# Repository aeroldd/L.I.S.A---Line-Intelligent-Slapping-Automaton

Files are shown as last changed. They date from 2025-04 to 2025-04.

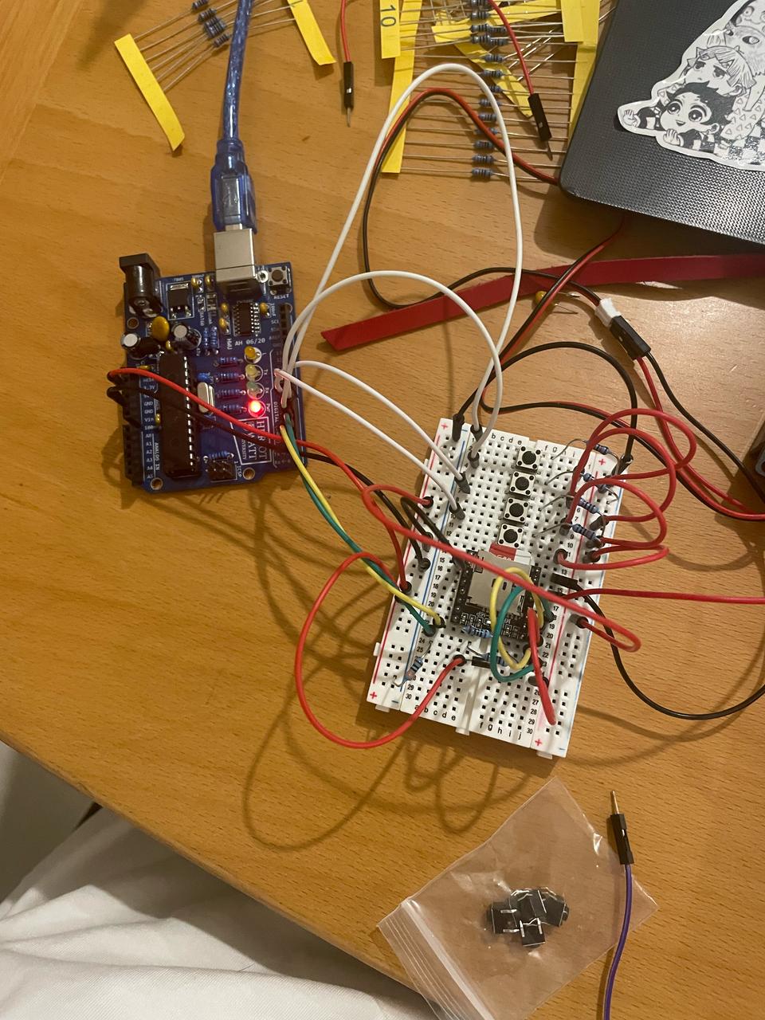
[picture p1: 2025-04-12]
Pictures/090325-DFPlayerMiniTestingB.jpg

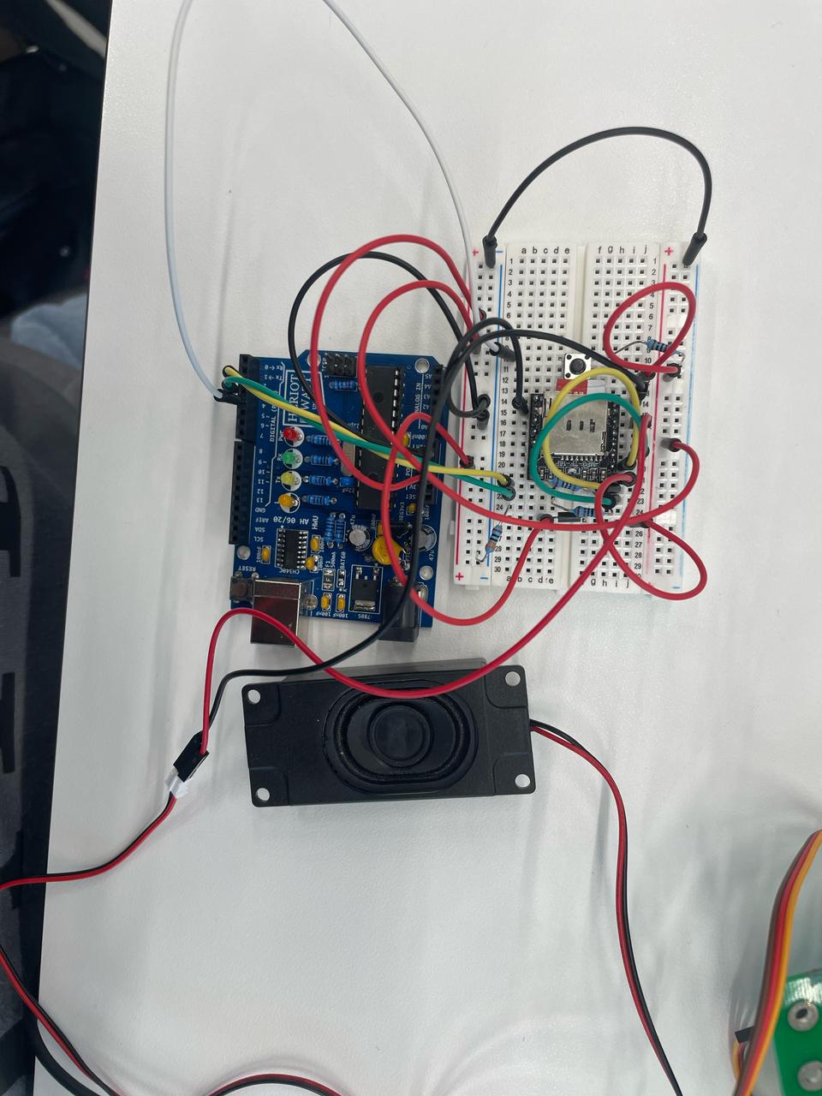
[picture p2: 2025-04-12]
Pictures/100325-DFPlayerMiniTesting.jpg

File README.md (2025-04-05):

L.I.S.A - Your Line Intelligent Slapping Automaton

Aerold Parcon and Anas Gomaa's brain child (Heriot Watt University - 1st Year Robotics Group Project B37VR Final Project)

Meet L.I.S.A - an intelligent robot controlled by an Arduino Uno that:
- Follows lines with a high degree of accuracy and precision
- Avoids obstacles by slapping them out of her way
- Has audio and visual cues to show what its doing
- Has lots of attitude

This repository houses all:
- All of L.I.S.A's brains (Arduino sketches used to control L.I.S.A's systems)
- Testing code and all the individual systems used in designing the final source code
- Sketches, CAD files and diagrams of the body and chasis
- Schematics of all sorts (Circuits, systems, etc)
- Your personal - How to make your own L.I.S.A instruction handbook.
- L.I.S.A care guide

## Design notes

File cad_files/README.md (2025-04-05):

THE CAD FILES OF L.I.S.A's Body and other printed parts

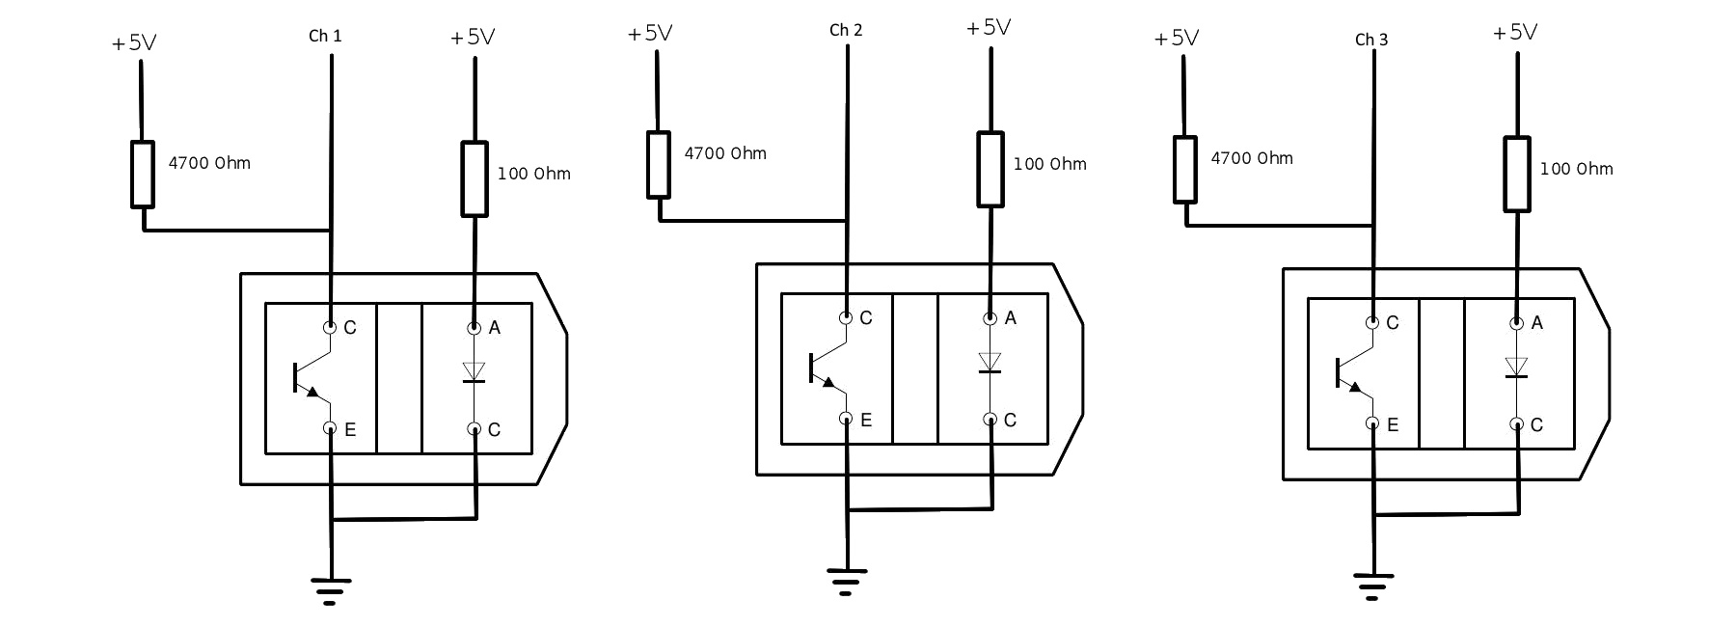
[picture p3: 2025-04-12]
Schematics/line follower module schematic.jpg

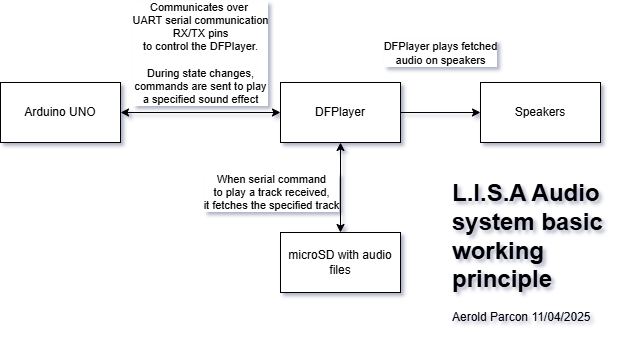
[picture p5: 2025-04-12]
Schematics/lisa_audio_system_blocks.drawio.png

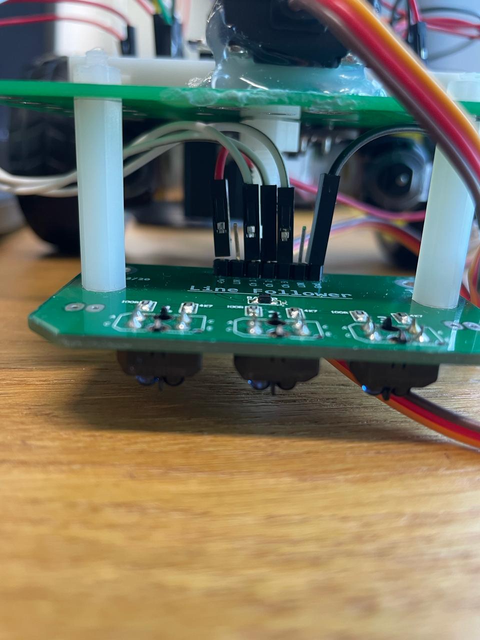
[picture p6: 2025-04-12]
Pictures/130325-LineFollowerPCBConnectedA.jpg

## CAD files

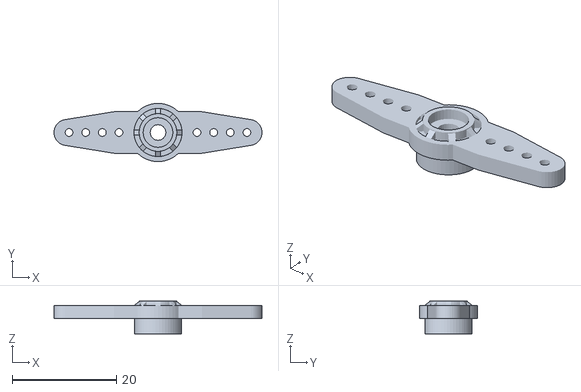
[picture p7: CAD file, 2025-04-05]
cad_files/mg996_arm_2pad.stl
40.0 x 11.2 x 6.30

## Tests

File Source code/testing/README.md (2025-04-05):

The main sketches used in the testing and calibration of L.I.S.A's development and prototyping time

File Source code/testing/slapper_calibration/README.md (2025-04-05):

SLAPPER CALIBRATION
This sketch is used to calibrate the minimum and maximum angle for slapping in L.I.S.A's obstacle avoidance system.
The right minimum and maximum angles must be determined so that the internal support structures in the chasis wouldnt get slapped on the way.

This sketch uses a potentiometer to set the angle and a button to confirm the angle
Once the program is finished running, the program prints out the minimum and maximum angles of the slap.
These values will be used in the slapper arm in the final L.I.S.A source code.

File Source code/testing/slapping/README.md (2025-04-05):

This sketch was used in testing the slapping mechanism of L.I.S.A.

Uses an ultrasonic sensor -> gets the distance -> if the distance is in the sapping threshold, it will slap the object infront of it.

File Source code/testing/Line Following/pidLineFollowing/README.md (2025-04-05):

/*
PID implemented Line following control of two Bi-directional Motors

This sketch was used to test if PID line following was better to use instead of a standard line
following agorithm - which it was

*/
// WheelDrive - move a pair of DC motors at varying rate and direction
//
// Copyright (c) 2016, Garth Zeglin.  All rights reserved. Licensed under the
// terms of the BSD 3-clause license as included in LICENSE.
//
// This program assumes that:
//
//  1. A DRV8833 dual DC motor driver module is connected to pins 5, 6, 9, and 10.
//  2. A pair of motors is attached to the driver.
//  3. The serial console on the Arduino IDE is set to 9600 baud communications speed.

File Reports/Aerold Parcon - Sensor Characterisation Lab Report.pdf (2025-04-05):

B37VR Robotics Group Project, Sensor characterisation report

# Heriot-Watt University Dubai

### B37VR Robotics Group Project, Year 1

## IR Sensor Characterisation Report

Student’s name | Aerold Parcon
Student ID | H00448855
Professor’s name | Dr Girish Balasubramanian
Buggy Number | B8

## Abstract

IR sensors are the eyes of an autonomous line following robot. The sensor’s characteristics must be understood to find the right thresholds of what the robot considers a line to follow. The experiments aimed to investigate IR sensor readings on different types of surfaces – grey floor, clean black tape and dirty black tape - and under different lighting conditions. An Arduino program was used to read the three IR sensor’s values. The results found that black tape, whether clean or dirty, produce a higher IR sensor reading than the grey floor. Increased ambient lighting increased the sensor reading in the grey floor, however this wasn’t observed in all surfaces, due to uncontrolled ambient lighting. The line following threshold values were found – the line is detected on values above 674. However, with the limited setup, the effects of ambient light and distance couldn’t be found.

## Contents

## Introduction

IR sensors are a core component of an autonomous line following robot. It serves as the ‘eyes’ of the robot, determining where the line is, and sends the recorded data to the Arduino Uno microcontroller which computes and updates the direction of the buggy. The TCRT5000 sensor used in this experiment is a reflective sensor which includes an infrared emitter and a phototransistor [1], and detects black lines by determining the amount of light which is reflected back (black absorbing more light than other surfaces).

In order to detect lines, a threshold of what is a black surface must be determined. This lab report aims to characterise the TCRT5000 sensor to determine the analog read values of different surfaces to define the sensing threshold of the black line to be followed and to analyse how the sensor’s readings are affected by different variables such as ambient light, the quality and texture of the surface. By the end of these series of experiments, the sensor’s characteristics will be determined and understood and the appropriate line reading threshold will be found.

Objectives:

- Understand the working principle of the TCRT5000 IR sensor.
- Test different surfaces against the IR sensor and find the right threshold for line following.
- Evaluate the effects of ambient lighting on the accuracy of the IR sensor.

## Background Theory - How IR sensors work and how it can detect lines

As briefly mentioned in the introduction, the TCRT5000 sensor is a reflective optical sensor with a transistor output, including an infrared emitter and a phototransistor [1].

The diagram below (Figure 2.1) is the circuit schematic of the sensor and how its used to read values.

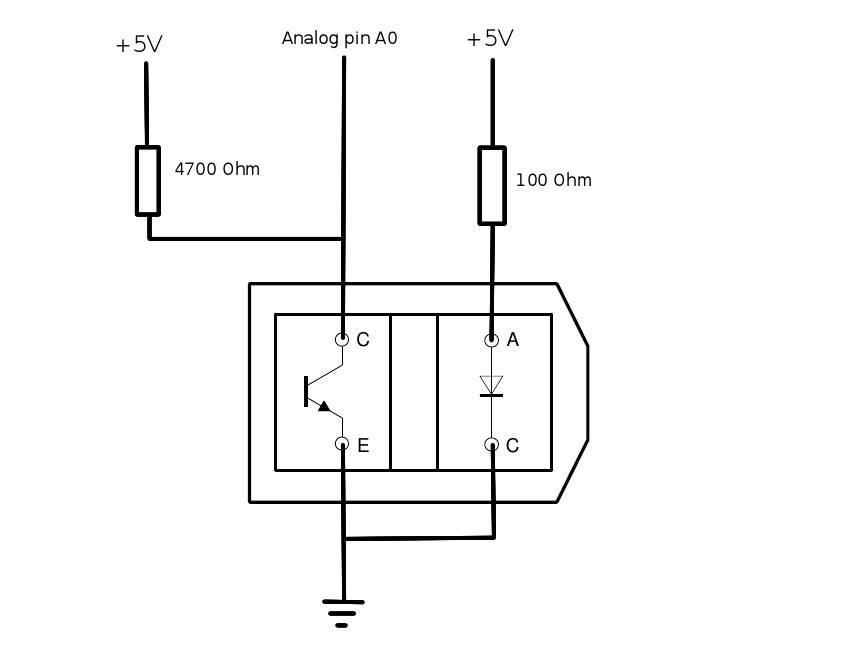
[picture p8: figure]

Figure 2.1: Top-down schematic view of the IR sensor, and how its connected to the Arduino analog pin A0 to read the sensor. [2]

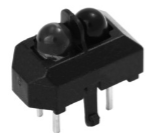
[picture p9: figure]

Figure 2.2: The TCRT5000 sensor. The black wall between the phototransistor and the IR LED blocks the emissions directly from the LED so that it can only detect the waves reflected back by surfaces. Image from the data sheet [1].

Essentially, the LED between points A and C shown on the figure above is an Infrared LED which emits a wave of 950nm [1]. The wave is emitted and is reflected on a surface, back to the sensor. The phototransistor detects the reflected infrared light – when light falls on the transistor, the atoms in the collector region become excited and emit free electrons [3], allowing current to flow through from the collector to the emitter. Therefore, as more light is detected, more atoms get excited and more electrons are freed, allowing more conductivity. This will cause more current to flow to the ground. This reduces the output voltage at point C, producing lower values.

In summary:

- IR LED emits light
- Light reflected and sensed by the phototransistor
- When the transistor detects light – more current flows to ground, less current flows to analog pin
- Therefore, more light = smaller reading; less light = greater reading.

## Methodology

In this lab report, various experiments were taken to characterise the IR sensor under different operating conditions - types of surfaces, and how the sensor reacts to different environmental ambient lighting. With the results gathered from these experiments, the line following threshold can be found.

Experimental setup

The following experiments were done using the Robotics Group Project buggy (Figure 3.1) provided by the course. It includes an Arduino Uno microcontroller, a breadboard for connections, an H-Bridge motor driver and a pair of motors (not used in this experiment), and a line following module – a PCB consisting of three TCRT5000 sensors, which are going to be characterised in these experiments.

The following connections were made (as shown on figure 3.2). 5V connected to the +5V pin on the Line Follower, channel 1, 2 and 3 connected to analog pins A3, A4 and A5 respectively and GND connected to GND. The fully wired IR sensor reading setup is shown on figure 3.3 below.

Figure 3.1: Arduino buggy used in this experiment. Other connections and modules were connected to the Arduino for other functionalities in the line following buggy – these can be ignored.

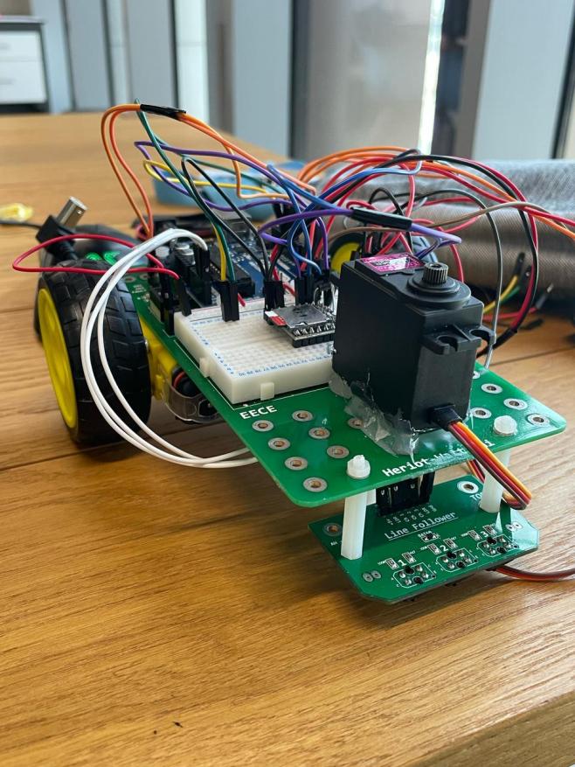
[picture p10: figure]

Figure 3.2: Schematic diagram of the IR sensor reading experimental setup.

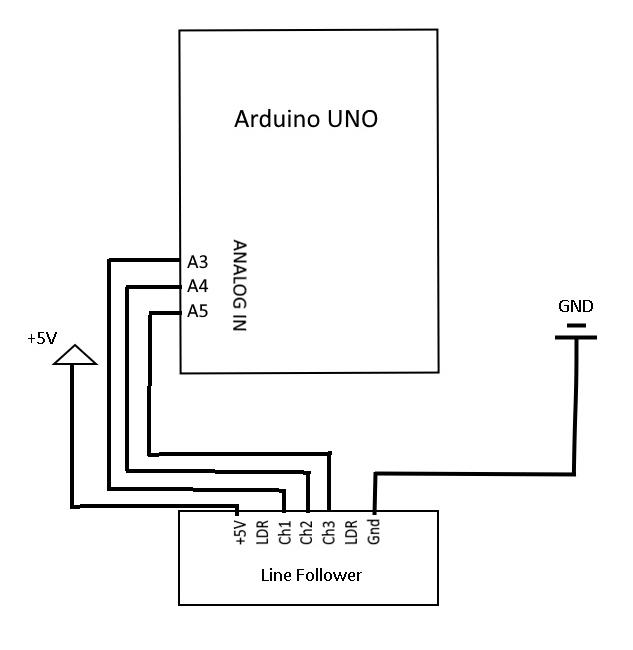
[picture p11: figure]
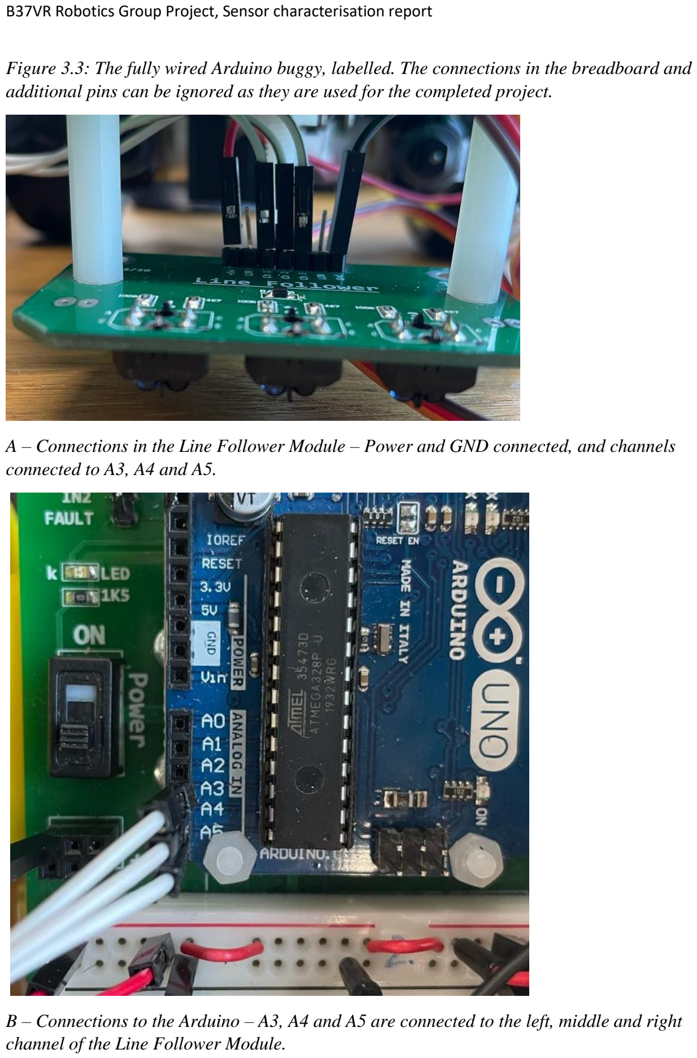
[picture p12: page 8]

Figure 3.3: The fully wired Arduino buggy, labelled. The connections in the breadboard and additional pins can be ignored as they are used for the completed project.

A – Connections in the Line Follower Module – Power and GND connected, and channels connected to A3, A4 and A5.

B – Connections to the Arduino – A3, A4 and A5 are connected to the left, middle and right channel of the Line Follower Module.

The Line Follower PCB
As previously mentioned, the three TCRT5000 sensors are soldered onto a PCB. The schematic diagram of the Line Follower module is attached on Appendix A. In summary, channel 1, 2 and 3 is connected to the collector pins of the left, centre and right sensors, and these are connected to the Arduino Uno’s A3, A4 and A5 analog pins.

Arduino code – IRSensorRead.ino

The sketch IRSensorRead.ino (full code available on Appendix B) is uploaded onto the Arduino Uno. It reads each channel’s analog output using analogRead(), an inbuilt function which reads the voltage in the analog pins as a value between 0-1023 bits. To convert this value into voltage, the following equation can be used:

V =

Analog read value + 1
1024

× 5

The program outputs the values in the format <left value>,<middle value>,<right value> on the Serial Monitor, which can be easily copied and pasted into a .csv file, which can later be opened in Excel for data analysis.

Surfaces

Figure 3.4: The different surfaces that will be tested in the experiments.

Type of Surface | Reason
Grey floor of robotics lab | Line following buggy demonstration will be carried out on the floor of the Robotics lab.
Glossy black electrical tape | Line following buggy designed to follow standard glossy black electrical tape on the floor of the Robotics lab.
Dirty dull black electrical tape | To test the tolerances the threshold should include. There may be imperfections in the line, so a dirty dulled out black electrical tape can serve as an extreme corner case for imperfections.

Figures 3.5 – 3.7 are pictures of the surfaces measured in this experiment.

Figure 3.5: Grey floor of the Robotics Laboratory

Figure 3.6: Clean black tape

Figure 3.7: Dirty black tape

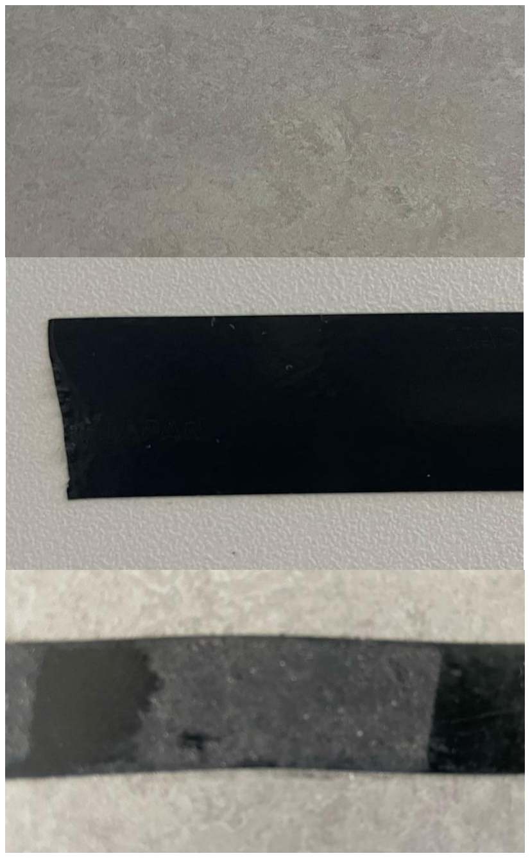
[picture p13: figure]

For the setup used in the experiments, strips of tape were placed on the ground.

Ambient lighting

To measure the IR sensors’ readings, the environment had to be as controlled as possible – the background lighting of a room interferes with the IR sensor readings. The ambient light had to be controlled as much as possible. Ideally, a totally dark environment should be used to eliminate the variable of ambient lighting. However, there were no totally dark areas in university where the experiment could be done, so two different light settings were chosen – dim and bright.

In previous experiments, the light intensity was measured with a luxmeter [4], and the correlation between light intensity and accuracy was found. However, due to limited resources, no light intensities could be quantified.

Lighting | Description
Dim | All lights in the Robotics Lab were dimmed to the lowest possible setting. Blinds and curtains were fully closed. The experiment was set up in a place far away from windows and other potential light sources.
Bright | All lights in the lab were set to the brightest setting. Blinds and curtains were fully drawn open to let as much sunlight in. However, the experiment was done in the same place so that the surfaces will be the same.

Figure 3.5: Two different lighting conditions that were controlled.

Distance

Initially, the effect of height on the IR sensor’s readings were to be investigated to find the optimal distance of the IR sensor from the ground for line following. Previous experiments [4] on IR sensor characteristics have done this using a custom-made jig, to measure the effects of distance to accuracy and precision. However, with the limited resources available, there were no ways to change the height accurately. In previous attempts, soldering helping hands were used to suspend the sensor and change the heights, but there was no proper way to repeat heights for experiments as there was a lot of human error – the angle, positioning, different heights, etc.

For this experiment, height was kept constant by attaching the Light Follower module to the buggy. This will be the same height used for line following, so it was practical.

Procedure

The experiment was first setup as described above – Code uploaded onto the Arduino, connections between the analog pins and the Line Follower module’s channels were made, surfaces were laid out, and ambient lighting were set.

The first experiment’s goal was to determine the IR sensors’ readings on each surface in the controlled dim light environment.

1) The readings for the floor were tested. The program was allowed to loop until approximately 20 sets of values were on the Serial Monitor in Arduino IDE.
2) These values were copied and recorded onto a CSV file.
3) This is repeated for the different surfaces – the clean glossy black electrical tape, and the dull dirty black electrical tape.

The second experiment’s goal was to investigate the effects of ambient room lighting on the IR sensors’ readings. The first experiment was repeated, but this time, instead of having the room’s lights dimmed, the lights were maximised to the brightest setting, and the windows were drawn open.

## Results

This section of the report presents the results of the IR sensor characterisation experiments, showing the effects of surface type and ambient light on the three sensors’ readings. The collected data (raw data available on Appendix C) includes the type of surface, the ambient lighting of the room, the average analog pin readings from the sensor, the average voltage, the minimum and maximum readings and standard deviation. The key findings are summarised in figures 4.1 to 4.4 below.

Figure 4.1: The effects of ambient lighting and surface type on IR sensor readings

Ambient Lighting | Surface type | Mean analog pin reading | Minimum analog pin reading | Maximum analog pin reading | Range
dim | Grey floor | 413.03 | 360.00 | 489.00 | 129
dim | Black tape (clean) | 865.23 | 838.00 | 899.00 | 81
dim | Black tape (dirty) | 905.73 | 802.00 | 965.00 | 163
bright | Grey floor | 436.39 | 373.00 | 541.00 | 168
bright | Black tape (clean) | 855.26 | 826.00 | 882.00 | 56
bright | Black tape (dirty) | 818.13 | 710.00 | 946.00 | 236

Figure 4.2: A minimum-maximum chart comparing the effects of lighting and surface on the IR sensor readings.

The standard deviation of the analog readings provides a measure of the IR sensor’s precision under different working conditions.

Figure 4.3: The average standard deviation of analog readings depending on the lighting and surface conditions.

Lighting Surface Average standard
deviation | Range
dim | grey | 0.88 | 129
dim | clean | 2.79 | 81
dim | dirty | 8.75 | 163
bright | grey | 1.24 | 168
bright | clean | 1.05 | 56
bright | dirty | 2.41 | 236
413.03 | 436.39
865.23 | 855.26

905.73

818.13

360 | 373
838 | 826 | 802

710

489

541

899 | 882
965 | 946

300.00

400.00

500.00

600.00

700.00

800.00

900.00

1000.00

dim | bright | dim | bright | dim | bright
grey floor | black tape (clean) | black tape (dirty)

### Effect of ambient light and surface type on IR sensor analog readings

Mean | Min | Max

Figure 4.4: The average standard deviations, graphed.

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
dim | bright | dim | bright | dim | bright
grey floor | black tape (clean) | black tape (dirty)

### Average standard deviation

## Discussion

This study investigated the effects of ambient background lighting and surface conditions on IR sensor readings. The results show that the sensor readings varied significantly based on the different factors – ambient lighting and surface type.

The results support the initial hypothesis - both clean and dirty black tape yielded higher readings than the floor as they reflect less light back. For example, when under dim light conditions, the floor returned an average reading of 413.03, compared to the higher readings of clean (865.23) and dirty black tape (905.73). Surface colour does affect the amount of infrared radiation absorbed as previously hypothesised, however, the type of surface – the reflectivity and smoothness – should also be accounted for. The black tape has a glossy finish which makes it act essentially as a mirror. Mirror reflection occurs when light strikes surfaces that are smooth or glossy, like the glossy black tape, reflecting at the opposite direction from the source [5]. Though the tape was glossy, because it was black, more infrared light was absorbed, hence giving a higher reading.

The uniformity and texture of the surface influences the IR sensor readings. The sensor readings were different when testing out clean and dirty tape surfaces. Under dim light conditions, the clean tape produced an average reading of 865.23, whereas the dirtier tape returned an average reading of 905.73. This is because the different dust and dirt particles in the dirty tape creates an uneven surface with different heights and colours, causing light to reflect in different directions, therefore less light is detected by the sensor.

The dirtier tape provided a greater range of readings, proving the influence surface texture has on sensor precision and accuracy. The clean tape has an average standard deviation of 2.76, while the dirty black tape has an average standard deviation 8.75, meaning that it read a wider range of values. As previously mentioned, this is because of the uneven surface with different heights, colours and reflectivity because of dust and dirt particles, reflecting light in different directions, which gives a wider range of values.

Different ambient light conditions affect sensor readings. For the grey floor, brighter room conditions increased the sensor readings compared to the dimmer room. Under dim light, the sensor read 413.03 on average, and under brighter light, the sensor read 436.39. Hypothetically, the reading should be lower because the IR sensor would detect more light from the environment, but that isn’t the case. This can be an anomalous reading. For the other surfaces, the results were as expected – for the clean black tape, it read 865.23 in dim light decreasing to 855.26 in bright light. This is because more IR light is detected from the surroundings, hence the lower reading. This is similar for the dirty tape (905.73 in dim, 818.13 in bright).

Interestingly, brighter room conditions increased the precision of reading black tape readings. Under dim light, the clean and dirty tape, had average standard deviations of the clean and dirty black tape were 2.79 and 8.75 respectively. Comparatively, under bright light, the clean and dirty tape, on average, had standard deviations of 1.05 and 2.41. The inconsistencies of the readings could be because the ambient lighting in the room couldn’t be perfectly controlled – non-uniform lighting, large windows on two sides of the room, position of the sun in the experiment, shadows, flickering room lights, etc. Therefore, the results fail to establish a relationship between ambient light and the precision and readings of the IR sensors – showing the importance of having a controlled laboratory environment for future iterations of this experiment.

For future experiments to investigate the effect of ambient light, a luxmeter should be used to measure the actual lighting on the room and find a correlation between the ambient lighting and sensor noise. A controlled environment where the lighting can be controlled should be used. To test the IR sensors without ambient light interference, the experiment must be done in a dark room.

Using the results, the global minimum and maximum thresholds for detecting surfaces can be finally determined. This is displayed on figure 5.1.

Figure 5.1: The line following thresholds.

Surface | Min | Max | Min -5% | Max+5%
Floor | 360.00 | 541.00 | 342 | 568
Line | 710.00 | 965.00 | 674 | 1013

## Conclusion

The aim of this lab report was to characterise a set of IR sensors to calibrate it and find an appropriate threshold for line detection for the line following buggy. The experiments and research carried out in this study successfully provided insight on the working principles of how IR sensors can be used to detect lines for an autonomous line following robot. The experiments aimed to investigate the influence of surfaces and ambient lighting on IR sensor readings, and it concluded that darker surfaces reflect less light, producing a greater IR sensor reading. With the limited experimental setup, the effects of ambient lighting on the IR sensor’s precision couldn’t be properly investigated as the room’s lighting couldn’t be quantified.

The ideal line detection thresholds have been successfully found in this experiment. This can be applied to the line following code to ensure precise line detection.

For future iterations of this study, a controlled environment where the ambient lighting can be measured and tweaked should be used to mitigate the errors caused by uncontrolled ambient light. Additionally, conducting the test in a fully darkened room can stop the ambient IR interference, or enclose it in a box. A lux meter should be used to measure the light intensity of ambient light.

Studying the effects of distance and angle from the surface can provide further insight to how it affects IR sensor readings, and using the results from the testing can give the ideal sensor position for line following, sensor sensitivity, noise and precision.

Now that the IR sensors were characterised, it can be used to make an autonomous line following robot.

## References

[1] Vishay Semiconductors (2009). TCRT5000, TCRT5000L Data sheet - Reflective Optical Sensor with Transistor Output. [Component data sheet] [Online] Available at: https://www.vishay.com/docs/83760/tcrt5000.pdf (Accessed at: 7th March 2025).
[2] B37VR Robotics Group Project (2025). TCRT5000 connection diagram - tcrt5000-connection.jpg. [Canvas] Available at: tcrt5000-connection.jpg. (https://canvas.hw.ac.uk/courses/27298/files/3903260/download?wrap=1) (Accessed at: 7th March 2025).
[3] Bishop, O. (2001) ‘Optoelectric Sensors’, in Understand Electronics. Newnes, pp. 131–137.
[4] B. Azzopardi, E. Dimech, A. Sammut and A. Mifsud (2023). "Characterisation of Infrared Sensors for Close-Proximity Distance Measurement," IECON 2023- 49th Annual Conference of the IEEE Industrial Electronics Society, Singapore, Singapore. pp. 1-6. Available at: doi 10.1109/IECON51785.2023.10312588. (Accessed at 11th Match 2025)
[4] 3M (2004) Reflectivity flyer, [Flyer] [Online PDF] Available at: https://multimedia.3m.com/mws/media/295767O/reflectivity-flyer.pdf. (Accessed at: 13th March 2025).

## Appendix

Appendix A – Line Follower PCB circuit diagram

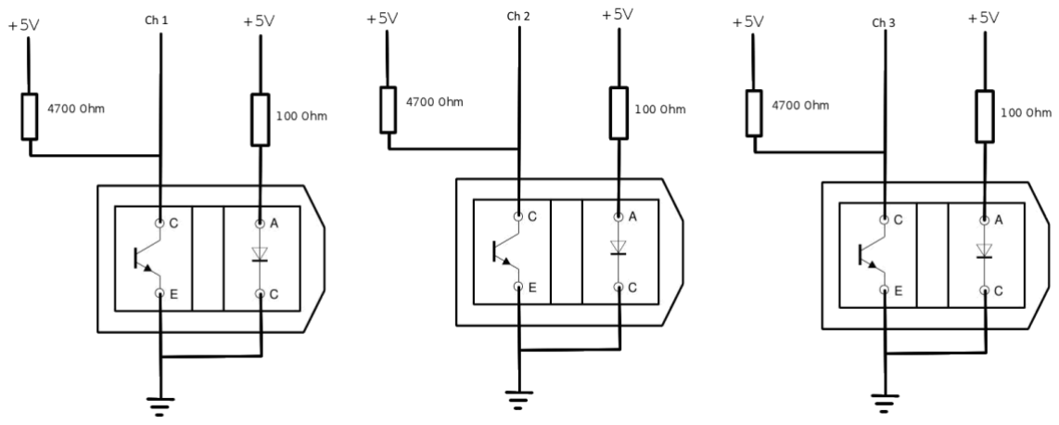
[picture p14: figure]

Figure A.1: Line Follower PCB circuit diagram. Consists of three IR sensors next to each other, and has pins Ch 1, Ch 2 and Ch 3 which are connected to the Arduino.

Appendix B – IRSensorRead.ino
The code below is a modified version of the sketchIRsensorRead.txt code taken from Canvas – changing it so that the printed values are in a .csv format for ease of data analysis in Excel.

/*
Read 3 IR sensors for callibration
*/
// Read 3 IR sensors for callibration //
/*
AnalogReadSerial

Reads an analog input on pin 3,4 &5, prints the result to the Serial Monitor. Graphical representation is available using Serial Plotter (Tools > Serial Plotter menu).

Adapted from the example code is in the public domain.

http://www.arduino.cc/en/Tutorial/AnalogReadSerial
*/

// the setup routine runs once when you press reset:
void setup() {
// initialize serial communication at 9600 bits per second: Serial.begin(9600);
}

// the loop routine runs over and over again forever: void loop() {
// read the input on analog pin 0:
int sensorValueLeft = analogRead(A5);
delay(2);
int sensorValueCentre = analogRead(A4); delay(2);
int sensorValueRight = analogRead(A3); delay(2);
// print out the value you read: Serial.print("");
Serial.print(sensorValueLeft); Serial.print(",");
Serial.print(sensorValueCentre); Serial.print(",");
Serial.println(sensorValueRight);
delay(1000); | // delay in between reads
}

Appendix C: Raw data summary
Sensor Position | Lighting | Surface | Average analog reading | Standard deviation | Voltage (average) | Min | Max
left | dim | Grey floor | 362.00 | 0.97 | 1.77 | 360.00 | 365.00
| | Clean black tape | 846.56 | 2.85 | 4.13 | 838.00 | 852.00
| | Dirty black tape | 833.70 | 8.81 | 4.07 | 802.00 | 840.00
| bright | Grey floor | 374.90 | 1.58 | 1.83 | 373.00 | 382.00
| | Clean black tape | 828.72 | 1.05 | 4.05 | 826.00 | 831.00
| | Dirty black tape | 795.63 | 3.22 | 3.88 | 784.00 | 799.00
middle | dim | Grey floor | 390.00 | 0.89 | 1.90 | 389.00 | 393.00
| | Clean black tape | 855.48 | 2.82 | 4.18 | 847.00 | 861.00
| | Dirty black tape | 925.07 | 8.68 | 4.52 | 895.00 | 931.00
| bright | Grey floor | 396.30 | 1.13 | 1.94 | 395.00 | 400.00
| | Clean black tape | 858.24 | 0.82 | 4.19 | 857.00 | 860.00
| | Dirty black tape | 715.43 | 1.84 | 3.49 | 710.00 | 717.00
Right | dim | Grey floor | 487.10 | 0.79 | 2.38 | 486.00 | 489.00
| | Clean black tape | 893.607 | 2.69 | 4.36 | 885.00 | 899.00
| | Dirty black tape | 958.43 | 8.74 | 4.68 | 928.00 | 965.00
| bright | Grey floor | 537.97 | 1.02 | 2.63 | 537.00 | 541.00
| | Clean black tape | 878.83 | 1.29 | 4.29 | 874.00 | 882.00
| | Dirty black tape | 943.33 | 2.17 | 4.61 | 936.00 | 946.00

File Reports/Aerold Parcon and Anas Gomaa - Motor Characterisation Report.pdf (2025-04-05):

B37VB Praxis Programming - Motor Characterisation Report

# Heriot-Watt University Dubai

Praxis Programming B37VB, Year 1

## Motor Characterisation Report

Student’s name | Aerold Parcon (H00448855)
Student’s name | Anas Gomaa (H00481128)
Group number (Buggy number) | B8
Professor’s name | Dr Girish Balasubramanian

### Table of contents

Introduction | 3
Aim | 3
Objective | 3
Methodology | 4
Buggy set up | 4
Experimental setup | 6
Identifying the deviation when the PWM values are set the same on the motors for three
speed settings | 7
Determining the corrected PWM values for the three speed settings | 7
Determining the speed (in m/s) for each corrected speed settings | 8
Results | 9
Discussion | 11
Conclusion | 13
References | 14
Appendices | 15
Appendix A - Code used for running the motors in different PWMs | 15
Appendix B - Raw data | 19

### Introduction

Motors drive the world to move - vehicles, various machines and mechanisms, robotics and various electrical engineering applications. However, you can’t just simply connect motors to anything without extensive characterisation - slight variations in motor characteristics, differences in power consumption (Kuphaldt and Haughery, 2020), or misalignment of motors with wheels, in addition to external conditions such as load variations, friction, or humidity, can greatly affect performance (Mabuchi Motor, n.d.). If motors aren't properly tested and characterized, malfunctions, instability, and potential hazards can occur. These hazards include road safety risks and dangerous accidents. Realistically, components don't perform as their datasheets indicate. Characterising all motors under all actual conditions is important to guarantee dependable performance.

The experiment's goal is to run multiple experiments to figure out all the buggy's motor characteristics - its deviation, its various speeds under different settings and conditions, as well as the correct values to use to ensure the correct operation of the buggy.

Aim
The aim is to characterise DC motors in an Arduino Uno buggy and to identify the right PWM values in order for the buggy to run as straight as possible. The buggy's speed should be measured at low, medium, and high PWM settings.
One must analyze trajectory deviations extensively at all speeds to carefully evaluate every difference between the motors.
To fully achieve the straightest movement possible, calculate corrected PWM values that minimize deviations.

Objective
1- Characterize the differences in speed between the two motors . 2- Correcting the PWM values
3- Calculate the speed of the buggy

### Methodology

Three different experiments were used to find the buggy’s deviation when using the same PWM values, to calibrate the DC motors to make it run as straight as possible, and to calculate the different speeds depending on the speed levels - low, medium and high.

Buggy set up
Prior to characterising the motors in the buggy, the buggy was set up to run the motors with set PWM values for each DC motor. The buggy was already pre-assembled with an Arduino Uno and an H-Bridge driving the motors, so the only thing left to do was to connect the motors and the Arduino Uno together.

The following connections (as shown on figures 2.1 and 2.2) were made.

Figure 2.1: Wiring diagram. Arduino PWM pins 5, 6, 10 and 11 connected to motor pins.

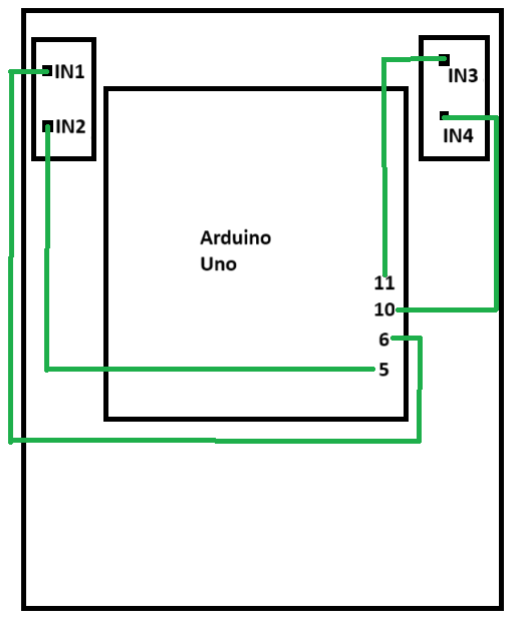
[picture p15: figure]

Figure 2.2: The buggy fully wired.

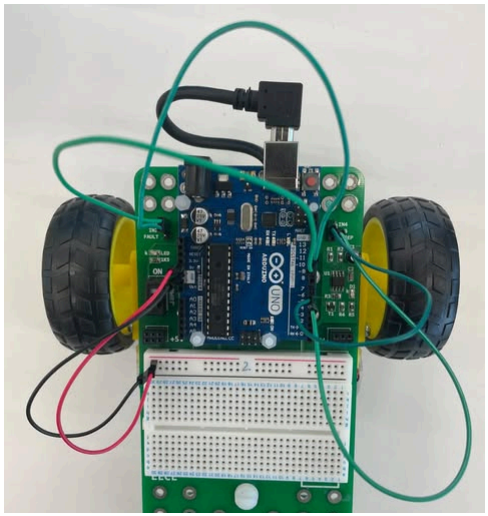
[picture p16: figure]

Uploading code

The code for motor control (available on Appendix A) was uploaded on the Arduino. This is taken from Code for driving motors available on Canvas (Zeglin, 2016). This code is modified so that the buggy can run at three different speeds - LOW, MEDIUM and HIGH. The variables leftServoSpeed and rightServoSpeed are changed across the experiments for different speeds and setting the corrected PWM values. The code block below shows the section of code where the speeds are changed.

/* variables for the speed of motors */
int leftServoSpeed = 100; // These values are changed int rightServoSpeed = 100; // Changed later on!!!

The default non tweaked speed settings used in the following experiments are as followed: LOW - 100 PWM - Any value lower than 80 isn’t enough to power the motors.

MEDIUM - 150 PWM
HIGH - 200 PWM

The corrected calibrated values for the left and right DC motors will be found and characterised in this experiment.

Now that the buggy was set up, the motor characterisation experiments can be done.

Experimental setup

Components needed:
- Fully set-up buggy
- Tape to mark the floor
- Phone camera
- Measuring tape

The following setup as shown on figures 2.3 was made on the floor of the Robotics Lab.

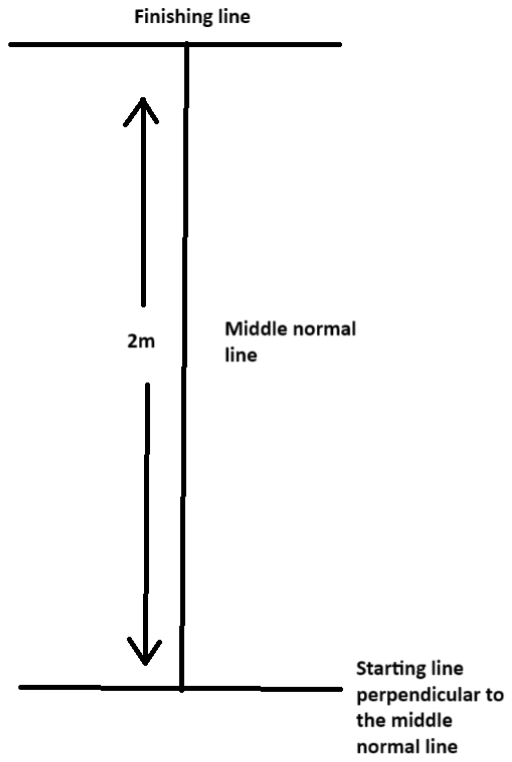
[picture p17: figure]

Figure 2.3: Diagram of the experimental setup used for this experiment. The lines were made using electrical tape.

It was made with the following steps:
1) Two points 2 meters apart were marked on the floor using the electrical tape. These points were connected with the tape, creating a line. This will be our reference line to determine the deviation.
2) Two lines perpendicular to the middle line were made. These are the starting and finishing lines.

Now that the lines were marked on the floor, it can be used to characterise the motors.

Procedure

Identifying the deviation when the PWM values are set the same on the motors for three speed settings

- The buggy was precisely aligned on the starting line using the perpendicular start line.
- The Arduino was programmed to set the motors with equal PWM values.
- The buggy was left to run for 5 seconds before stopping it to measure the deviation from the middle line.
- A camera was used to record the exact time the buggy will start and stop to ensure the constant 5 seconds. The stopping point of the buggy was also found using the recorded camera footage.This step was done to reduce human error.
- This was repeated for many runs to calculate the average deviation for each speed setting.

Determining the corrected PWM values for the three speed settings

As previously observed in the previous experiment, the buggy deviates greatly from the reference line, therefore the default speed PWM values need to be corrected in each wheel in order for the buggy to run as straight as possible.

1) The motors were set to the default PWM values in the Arduino Uno.
2) According to the previous results in the first experiment, the PWM values of the motors were tweaked. For example, if the buggy deviated to the left, rightServoSpeed would be increased and leftServoSpeed decreased in the code, and this would be uploaded again on the Arduino.
3) The buggy was aligned over the starting point, and powered on in the air to accelerate before placing it down. This is so that the slight difference and delay in the motor’s powering wouldn’t initially deviate the buggy. It was then set down to drive to the finish line. When it didn’t reach the finish line, the values were further tweaked. When the finish line was reached, the buggy was stopped, and the deviation from the middle line was recorded using measuring tape.
4) Depending on the deviation from the previous run, the PWM would be tweaked until it runs as straight as possible.
5) This is repeated for the different PWM speed settings LOW, MEDIUM and HIGH until all of them run as straight as possible.

Determining the speed (in m/s) for each corrected speed settings

Once the corrected values were calibrated onto the DC motors, the motors will be characterised by calculating the speed of the buggy in three different speed settings.

1) Motors were set to the corrected PWMs for a speed setting (low, medium or high) on the Arduino.
2) Phone camera was prepared to record the buggy.
3) Buggy was aligned over the starting point and allowed to accelerate in the air before placing it down.
4) Once placed down, the camera started recording at the same time.
5) Buggy is stopped once it reaches the finishing line, and the ending point is marked. The deviation is measured using measuring tape. The phone camera’s recording is stopped.
6) Using the recorded footage, the time taken to reach the end was measured precisely.
7) Speed is calculated using the time taken and the distance travelled
distance (m) = lengtℎ of track ²
+ deviation

2

speed = distance/time

The distance is calculated with Pythagoras Theorem (figure 2.4)


Figure 2.4: Diagram to show how the distance travelled is calculated with Pythagoras Theorem. The distance travelled is the hypotenuse of the triangle formed by the deviation and the distance between the starting and finishing line.

### Results

Raw data used to create these tables are in Appendix B. Multiple runs were taken to find the average deviation and speed. The tables below hold the results of the motor characterisation experiments.

Table 1: Average deviation when using the same PWM values
Speed | PWM left | PWM right | Average deviation from the normal (cm)
Low | 100 | 100 | 113.50
Medium | 150 | 150 | 189.75
High | 200 | 200 | 198.50

Table 2: Corrected PWM values and their speeds

Speed | PWM left | PWM right | Average PWM between the two motors | Average speed (m/s) | Average deviation from the normal (cm)
Low | 120 | 99 | 109.5 | 0.337 | 3.0
Medium | 163 | 137 | 150 | 0.465 | 9.0
High | 225 | 176 | 200.5 | 0.567 | 5.0

Figure 3.1: Average speed plotted against average PWM at each speed setting


### Discussion

Deviations and imperfections in the motors
Throughout all the experiments, the results show that there is a deviation - there were no trials where the buggy went perfectly straight, even when finding the corrected values. This is because the motors will have different power distributions due to difference in efficiency and small physical errors in its manufacturing, such as different magnet strengths inside the motor, friction between the gears and mechanical parts, and resistances. In these experiments, the left motor (when viewing it from the buggy facing you) was substantially weaker than the right motor. When the PWM values are the same for each speed setting, the buggy would always deviate to the right, and not even reach the finishing line on the other end of the setup. Upon further inspection in the experiments, the left motor is louder than the right motor, which can mean that there is more friction between the gears of the motor.

First experiment - as speed increases, deviation increases
In the first experiment where the deviations were measured after 5 seconds of running, there can be slight human error in determining the exact stop point of the buggy as we are judging the final position from the video. However it was decided to use the video to get position to keep the time constant as using a stopwatch for time introduces human error by reaction time and time won’t be constant.

As the speed is increased in the first experiment when the PWMs are set the same, there is a greater deviation. For example, at low speed setting there is an average of 113.50 cm deviation and at high setting, there is an average of 198.50cm. This could be due to the differences in power of the motors being amplified at higher PWMs.

Second experiment
No matter what values were entered, there were no values where the buggy would run perfectly straight. As mentioned previously this is because of the differences in the motors. However, even when calibrating the motors they wont run straight. For example, in Appendix B table 2, when the PWMs were changed from 163/137 to 164/137, the deviation itself changed from 9 cm to -10cm, which indicates that the correct PWM value is between the 163 and 164 for the left motor. To further improve the corrections of PWM values, float values should be used. However, in an Arduino Uno which is used in this project, PWM values only range from 0-255.

Third experiment - average speed and PWM
PWM and average speed of the buggy have a positive correlation - when PWM is increased, the speed is increased, just as shown on figure 3.1. This is because as there’s more power supplied to the motor, it will move faster. Using the graph on figure 3.1, the average PWM can be extrapolated if you want to have a specific average speed. For example, if you wanted the buggy to run at 0.5m/s, the approximate average PWM value will be 170, and from the 170 value, you further calibrate the values until it goes straight.

Other factors affecting deviation and human errors
There can be more reasons why there were deviations such as the unevenness and friction of the ground which could cause the buggy to tilt towards one direction. To keep this variable constant, we used the same setup on the same floor surface as the final project of this course.

The uneven weight distribution on the buggy due to the different components and wiring can cause deviations too. However the weight distribution must be negligible as the components are small. In future iterations of this buggy with extra modifications and body work, a counterweight can be implemented to ensure the equal weight distribution.

Another source of deviation can be the initial starting position and alignment. When placing the buggy at the starting point there can be a slight error where it’s not heading perfectly straight. Therefore, human error has affected the results gathered from this experiment. To try reducing human error, the starting point was marked with tape, and we ensured that the starting and finishing lines were perfectly perpendicular to the middle. In future experiments, a parallel set of guidelines can be used to ensure the perfect starting alignment of the buggy.

Additionally, the motors power on at a very slightly different time (the left motor being weaker powers later), and accelerate at a different rate. To avoid this issue, before setting the buggy down, it was allowed to accelerate in the air. However this can increase the human error due to the shaking and rattling of the buggy while it's in the air causing the starting position to be off, and the bouncing off the ground. But the initial deviation caused by the uneven starting times of the motors affected the results more, so this method was used.

To try reducing the error and accuracy of the results gathered, multiple runs were taken and averaged.
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

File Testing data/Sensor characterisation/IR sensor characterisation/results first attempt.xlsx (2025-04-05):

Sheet: Sheet1
 |  |  | Left |  | Middle |  | Right
Surface type | Height | trial | Analog pin reading | Voltage reading (v) | Analog pin reading | Voltage reading (v) | Analog pin reading | Voltage reading
Floor | 3mm | 1
 |  | 2
 |  | 3
 |  | average | #DIV/0! | #DIV/0! | #DIV/0! | #DIV/0! | #DIV/0! | #DIV/0!
 | 5mm | 1
 |  | 2
 |  | 3
 |  | average | #DIV/0! | #DIV/0! | #DIV/0! | #DIV/0! | #DIV/0! | #DIV/0!
 | 7mm | 1
 |  | 2
 |  | 3
 |  | average | #DIV/0! | #DIV/0! | #DIV/0! | #DIV/0! | #DIV/0! | #DIV/0!
 | 9mm | 1
 |  | 2
 |  | 3
 |  | average | #DIV/0! | #DIV/0! | #DIV/0! | #DIV/0! | #DIV/0! | #DIV/0!
Black tape | 3mm | 1
 |  | 2
 |  | 3
 |  | average | #DIV/0! | #DIV/0! | #DIV/0! | #DIV/0! | #DIV/0! | #DIV/0!
 | 5mm | 1
 |  | 2
 |  | 3
 |  | average | #DIV/0! | #DIV/0! | #DIV/0! | #DIV/0! | #DIV/0! | #DIV/0!
 | 7mm | 1
 |  | 2
 |  | 3
 |  | average | #DIV/0! | #DIV/0! | #DIV/0! | #DIV/0! | #DIV/0! | #DIV/0!
 | 9mm | 1
 |  | 2
 |  | 3
 |  | average | #DIV/0! | #DIV/0! | #DIV/0! | #DIV/0! | #DIV/0! | #DIV/0!
Black tape (dirty) | 3mm | 1
 |  | 2
 |  | 3
 |  | average | #DIV/0! | #DIV/0! | #DIV/0! | #DIV/0! | #DIV/0! | #DIV/0!
 | 5mm | 1
 |  | 2
 |  | 3
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

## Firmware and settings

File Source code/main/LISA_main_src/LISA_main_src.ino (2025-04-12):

/*
Line following control of two Bi-directional Motors
*/
// WheelDrive - move a pair of DC motors at varying rate and direction
//
// Copyright (c) 2016, Garth Zeglin.  All rights reserved. Licensed under the
// terms of the BSD 3-clause license as included in LICENSE.
//
// This program assumes that:
//
//  1. A DRV8833 dual DC motor driver module is connected to pins 5, 6, 9, and 10.
//  2. A pair of motors is attached to the driver.
//  3. The serial console on the Arduino IDE is set to 9600 baud communications speed.

// ================================================================================
// Define constant values and global variables.

#include <NewPing.h>
#include <Servo.h> 
#include <DFMiniMp3.h>
#include <SoftwareSerial.h>

// ===== MOTOR CONTROL PINS =====
#define MOT_A1_PIN 5
#define MOT_A2_PIN 6
#define MOT_B1_PIN 9
#define MOT_B2_PIN 10

// ===== SENSOR PINS =====
const int irPins[3] = { A5, A4, A3 };
#define TRIGGER_PIN 12
#define ECHO_PIN 13

// ===== SERVO CONTROL PIN =====
#define SERVO_PIN 3

// ===== LED CONTROL PIN =====
#define LED_CONTROL_PIN 7

// ===== AUDIO PINS =====
#define AUDIO_RX 2
#define AUDIO_TX 4

// ===== CONSTANTS =====
int threshold = 400;  // IR sensor threshold value for line detection
const int maxSpeed = 200;  // the range for speed is(0,255)
#define MAX_DISTANCE 200
#define STOP_THRESHOLD 10 // the buggy stops and slaps when the object is 15 cm or closer to the sensor

#define SPEAKER_VOLUME 30

#define WARNING_DURATION 250

// ===== GLOBAL VARIABLES =====
// motor global variables
boolean reverseL = 0;
boolean reverseR = 0;
int leftServoSpeed = 0;
int rightServoSpeed = 0;
const int motorOffset = 12; 

// binary representation of the sensor reading
// 1 when the sensor detects the line, 0 otherwise
int irSensorDigital[3] = { 0, 0, 0 };
int irSensors = B000;

// A score to determine deviation from the line [-180 ; +180].
// Negative means the robot is left of the line.
int error = 0;
int errorLast = 0;  //  store the last value of error

// Ultrasonic sensor distance global variables
NewPing sonar(TRIGGER_PIN, ECHO_PIN, MAX_DISTANCE); // NewPing setup of pins and maximum distance.
int distance;

// Define servo
Servo servo;

// Audio things
SoftwareSerial secondarySerial(4,2); // RX, TX
class Mp3Notify; 
typedef DFMiniMp3<SoftwareSerial, Mp3Notify> DfMp3;
DfMp3 dfmp3(secondarySerial);
int audioFinished;

// Class used to handle notifying stuff to the serial monitor

class Mp3Notify
{
public:
  static void PrintlnSourceAction(DfMp3_PlaySources source, const char* action)
  {
    if (source & DfMp3_PlaySources_Sd) 
    {
        Serial.print("SD Card, ");
    }
    if (source & DfMp3_PlaySources_Usb) 
    {
        Serial.print("USB Disk, ");
    }
    if (source & DfMp3_PlaySources_Flash) 
    {
        Serial.print("Flash, ");
    }
    Serial.println(action);
  }
  static void OnError([[maybe_unused]] DfMp3& mp3, uint16_t errorCode)
  {
    // see DfMp3_Error for code meaning
    Serial.println();
    Serial.print("Com Error ");
    Serial.println(errorCode);
  }
  static void OnPlayFinished([[maybe_unused]] DfMp3& mp3, [[maybe_unused]] DfMp3_PlaySources source, uint16_t track)
  {
    Serial.print("tester");
    Serial.print("Play finished for #");
    Serial.println(track);  
    audioFinished = 1;
  }
  static void OnPlaySourceOnline([[maybe_unused]] DfMp3& mp3, DfMp3_PlaySources source)
  {
    PrintlnSourceAction(source, "online");
  }
  static void OnPlaySourceInserted([[maybe_unused]] DfMp3& mp3, DfMp3_PlaySources source)
  {
    PrintlnSourceAction(source, "inserted");
  }
  static void OnPlaySourceRemoved([[maybe_unused]] DfMp3& mp3, DfMp3_PlaySources source)
  {
    PrintlnSourceAction(source, "removed");
  }
};

// ===== BUGGY STATES =====
#define MOVING 0
#define WARNING 1
#define SLAPPING 2

int state;
int previousState;
int warningCount = WARNING_DURATION;

// ================================================================================
void setup(void) {
  // Initialize the stepper driver control pins to output drive mode.
  pinMode(MOT_A1_PIN, OUTPUT);
  pinMode(MOT_A2_PIN, OUTPUT);
  pinMode(MOT_B1_PIN, OUTPUT);
  pinMode(MOT_B2_PIN, OUTPUT);

  // Start with drivers off
  digitalWrite(MOT_A1_PIN, LOW);
  digitalWrite(MOT_A2_PIN, LOW);
  digitalWrite(MOT_B1_PIN, LOW);
  digitalWrite(MOT_B2_PIN, LOW);

  // Initialize the serial UART at 9600 bits per second.
  Serial.begin(9600);

  // Initialize the servo motor to the 0 position
  pinMode(SERVO_PIN, OUTPUT);
  initServoMotors();

  // Initialize the ultrasonic sensors
  pinMode(TRIGGER_PIN, OUTPUT);
  pinMode(ECHO_PIN, INPUT);


  // Initialize the LEDS
  pinMode(LED_CONTROL_PIN, OUTPUT);
  // Blink once as a test
  digitalWrite(LED_CONTROL_PIN, HIGH);
  delay(1000);
  digitalWrite(LED_CONTROL_PIN, LOW);

  // Initialise the DFPlayerMini
  initDFPlayer();

  Serial.println("Buggy initialized.");
}

void initServoMotors() {
  newServoAttach(SERVO_PIN);
  servo.write(0);
  newServoDetach();
}

void initDFPlayer() {
  Serial.println("Initialising DFPlayerMini audio chip...");
  dfmp3.begin();

  uint16_t version = dfmp3.getSoftwareVersion();
  Serial.print("version ");
  Serial.println(version);

  uint16_t volume = dfmp3.getVolume();
  Serial.print("volume ");
  Serial.println(volume);
  dfmp3.setVolume(SPEAKER_VOLUME);
  
  uint16_t count = dfmp3.getTotalTrackCount(DfMp3_PlaySource_Sd);
  Serial.print("files ");
  Serial.println(count);

  playInit();
}

// ===== AUDIO PLAYING FUNCTIONS =====

int playInit() {
  playStartUp();
  playGreeting();
  delay(200);
}

int playStartUp() {
  audioFinished = 0;
  Serial.println("play start up noise");
  dfmp3.playFolderTrack16(1, 1);
  delay(100);
  waitForAudioToFinish();
  return 1;
}

int playGreeting() {
  audioFinished = 0;
  Serial.println("play greeting");
  dfmp3.playFolderTrack16(1,2);
    delay(100);
  waitForAudioToFinish();
  return 1;
}

int playLineFollowing() {
  audioFinished = 0;
  Serial.println("play line following");
  dfmp3.playFolderTrack16(2,1);
  delay(100);
  waitForAudioToFinish();
  return 1;
}

int playBeep() {
  audioFinished = 0;
  Serial.println("play beep");
  dfmp3.playFolderTrack16(3,1);
  return 1;
}

int playWarning() {
  audioFinished = 0;
  Serial.println("play warning");
  dfmp3.playFolderTrack16(3,2);
  delay(100);
  //waitForAudioToFinish();
  return 1;
}

int playSlapStart() {
  audioFinished = 0;
  Serial.println("play slap start");
  dfmp3.playFolderTrack16(3,3);
  delay(100);
  waitForAudioToFinish();
  return 1;
}

int playSlapFinish() {
  Serial.println("play slap finish");
  dfmp3.playFolderTrack16(3,4);
  delay(100);
  waitForAudioToFinish();
  return 1;
}

void waitForAudioToFinish() {
  DfMp3_Status status = dfmp3.getStatus(); // Get playback status
  Serial.println(status.state); // Print status as an integer
  if(status.state==0) {
    Serial.println("broken");
    status = dfmp3.getStatus();
  }
  while(status.state){
    status = dfmp3.getStatus();
    Serial.println("waiting for the track to finish");
    delay(100);
    dfmp3.loop();
  }
  dfmp3.loop();
  delay(100);
}

// ================================================================================
/// Set the current on a motor channel using PWM and directional logic.
/// Changing the current will affect the motor speed, but please note this is
/// not 3a calibrated speed control.  This function will configure the pin output
/// state and return.
///
/// \param pwm    PWM duty cycle ranging from -255 full reverse to 255 full forward
/// \param IN1_PIN  pin number xIN1 for the given channel
/// \param IN2_PIN  pin number xIN2 for the given channel

void set_motor_pwm(int pwm, int IN1_PIN, int IN2_PIN) {
  if (pwm < 0) {  // reverse speeds
    analogWrite(IN1_PIN, -pwm);
    digitalWrite(IN2_PIN, LOW);

  } else {  // stop or forward
    digitalWrite(IN1_PIN, LOW);
    analogWrite(IN2_PIN, pwm);
  }
}

// ================================================================================
/// Set the current on both motors.
///
/// \param pwm_A  motor A PWM, -255 to 255
/// \param pwm_B  motor B PWM, -255 to 255

void set_motor_currents(int pwm_A, int pwm_B) {
  set_motor_pwm(pwm_A, MOT_A1_PIN, MOT_A2_PIN);
  set_motor_pwm(pwm_B, MOT_B1_PIN, MOT_B2_PIN);

  //Print a status message to the console.
  // Serial.print("Set motor A PWM = ");
  // Serial.print(pwm_A);
  // Serial.print(" motor B PWM = ");
  // Serial.println(pwm_B);
}

// ================================================================================
/// Simple primitive for the motion sequence to set a speed and wait for an interval.
///
/// \param pwm_A  motor A PWM, -255 to 255
/// \param pwm_B  motor B PWM, -255 to 255
/// \param duration delay in milliseconds
void spin_and_wait(int pwm_A, int pwm_B, int duration) {
  set_motor_currents(pwm_A, pwm_B);
  delay(duration);
}

// IR sensor scanning - updates the irSensors global variable
void scanIR() {
  irSensors = B000;

  for (int i = 0; i < 3; i++) {
    int sensorValue = analogRead(irPins[i]);
    if (sensorValue >= threshold) {
      irSensorDigital[i] = 1;
      // Serial.print(1);
      // Serial.print(" ");
    }

    else {
      irSensorDigital[i] = 0;
      // Serial.print(0);
      // Serial.print(" ");
    }

    int b = 2 - i;
    irSensors = irSensors + (irSensorDigital[i] << b);
  }
}

// Ultrasonic sensor scanning - updates the distance global variable
void scanUltrasonic() {
  distance = sonar.ping_cm();
}

// PID Constants (Tune these values)
float Kp = 0.9;  // Proportional gain
float Ki = 0.0;  // Integral gain (usually small or 0)
float Kd = 0.2;  // Derivative gain

float integral = 0;
float derivative = 0;

void UpdateDirection() {
  
  errorLast = error;

  switch (irSensors) {
    case B000: // No sensor detects the line
       error = (errorLast < 0) ? -130 : 130;
       break;
    case B100: error = -100; break; // Leftmost sensor
    case B110: error = -50; break;
    case B010: error = 0; break; // Centered
    case B011: error = 50; break;
    case B001: error = 100; break; // Rightmost sensor
    case B111: error = 0; break; // Perfectly centered
    default:   error = errorLast;
  }

  // PID Calculation
  integral += error;                      // Accumulate integral (sum of past errors)
  derivative = error - errorLast;         // Rate of change of error
  float correction = (Kp * error) + (Ki * integral) + (Kd * derivative);

  // Adjust Motor Speeds
  leftServoSpeed = maxSpeed + correction;
  rightServoSpeed = maxSpeed - correction;

  // Keep Speeds within Valid Range
  leftServoSpeed = constrain(leftServoSpeed + motorOffset, 0, maxSpeed + motorOffset);
  rightServoSpeed = constrain(rightServoSpeed - motorOffset, 0, maxSpeed - motorOffset);
}

// Updates the buggy state global variable
void updateState() {
    // Check if an object is within the stop threshold
    previousState = state; // Update previous state for next cycle
    bool objectDetected = (distance <= STOP_THRESHOLD && !(distance == 0)); // If the object is in the stop threshold and not 0 (aka above the sensing range) it returns 1
    
    switch (previousState) {
        case MOVING:
            if (objectDetected) {
                state = WARNING;
            }
            break;
        
        case WARNING:
            if (!objectDetected) {
              state = MOVING; // Return to moving if object is gone
            } else if (warningCount == 0) {
              state = SLAPPING;
              playSlapStart();
            }
            break;
        
        case SLAPPING:
            if (!objectDetected) {
                state = MOVING; // Return to moving once object is gone
                playSlapFinish();
                //delay(2000);
                playLineFollowing();
                Serial.println("I am line following");
                warningCount = WARNING_DURATION;
            }
            else if (objectDetected) {
              state = SLAPPING;
              playSlapStart();
            }
            break;
    }
    
}

// When attaching a servo to the Arduino, the PWM pins 9 and 10 don't work. So this will attach the servo seperately only when the object is detected.
void newServoAttach(int pin) {
  // turn the motors off
  digitalWrite(MOT_A1_PIN, LOW);
  digitalWrite(MOT_A2_PIN, LOW);
  digitalWrite(MOT_B1_PIN, LOW);
  digitalWrite(MOT_B2_PIN, LOW);
  servo.attach(pin);
}

void newServoDetach() {
  servo.detach();
  // Reinitialize the stepper driver control pins to output drive mode.
  pinMode(MOT_A1_PIN, OUTPUT);
  pinMode(MOT_A2_PIN, OUTPUT);
  pinMode(MOT_B1_PIN, OUTPUT);
  pinMode(MOT_B2_PIN, OUTPUT);

  // Start with drivers off, motors coasting.
  digitalWrite(MOT_A1_PIN, LOW);
  digitalWrite(MOT_A2_PIN, LOW);
  digitalWrite(MOT_B1_PIN, LOW);
  digitalWrite(MOT_B2_PIN, LOW);

  // got this code from chatgpt but basically
  // the Servo.attach() function disables the PWM on pins 9 and 10 which controls the motors - so when
  // the servo is attached to the Arduino, the motors driving the buggy stop working
  // the code below reenables the PWM functionality of those pins.

  TCCR1A = _BV(COM1A1) | _BV(COM1B1) | _BV(WGM10);
  TCCR1B = _BV(WGM12) | _BV(CS11);
}

void slap() {
  // Attach the servo to pin 3
  newServoAttach(3);

  // Set the Servo to 180 degrees
  servo.write(180-40);

  // Slap the object for 1 second
  delay(1000);

  // Bring the servo back to the starting position
  servo.write(0+40);

  // 1 second delay
  delay(1000);

  // detach the servo from the pin and re-enable the PWM on pins 9 and 10
  newServoDetach();

  Serial.println("Object slapped!");
}

void lineFollowing() {
  // keep the same motor speed
  // check to see if the state was changed to MOVING - if so, the line following sound will play
  Serial.print("left: ");
  Serial.print(leftServoSpeed);
  Serial.print(" right: ");
  Serial.print(rightServoSpeed);
  spin_and_wait(leftServoSpeed, rightServoSpeed, 10);
  if(previousState != state) {
    Serial.println("change!");
    //playLineFollowing();
  }
}

void warning() {
  // stop buggy
  if(previousState != WARNING) {
    //playLineFollowing();
  }

  if(warningCount == WARNING_DURATION) {
    playWarning();
    //waitForAudioToFinish();
  }

  if(warningCount % 50 == 0) {
    ledFlip(7);
    playBeep();
  }

  spin_and_wait(0, 0, 10);
  if(previousState != state) {
  Serial.println("change!");

  }
  // decrement the warningCount by 1
  warningCount -= 1;
}

void slapping() {
  // stop the buggy
  spin_and_wait(0, 0, 10);
  slap();
}

void ledOn(int pin) {
  digitalWrite(pin, HIGH);
}

void ledOff(int pin) {
  digitalWrite(pin, LOW);
}

void ledFlip(int pin) {
  if(digitalRead(pin)) {
    digitalWrite(pin, LOW);
  }
  else digitalWrite(pin, HIGH);
}

void loop() {
  // get data from the IR and ultrasonic sensors
  scanIR();
  scanUltrasonic();

  // update the direction of the buggy depending on the sensor's data
  UpdateDirection();

  // update the buggy's state based on the sensor's data
  updateState();

  // do different functions based on the buggy's state machine
  switch (state) {
    case MOVING: {
      lineFollowing();
      Serial.print("FOllowing line");
      ledOn(7);
      break;
    }

    case WARNING: {
      warning();
      Serial.println(warningCount);
      Serial.print("Warning");
      break;
    }

    case SLAPPING: {
      // Slap the object!
      slap();
      Serial.println("slapping");
            ledOff(7);
      break;
    }
  }
  Serial.println(distance);
  dfmp3.loop();
}

}

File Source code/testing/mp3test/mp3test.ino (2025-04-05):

/*
Audio test - used to see if the DFPlayerMini chip and speaker set up even worked

This plays a beep every second.

Portions of this code is taken from the DFPlayer Mini example code
*/



#include <DFMiniMp3.h>
#include <SoftwareSerial.h>

// forward declare the notify class, just the name
//
class Mp3Notify; 

// Some arduino boards only have one hardware serial port, so a software serial port is needed instead.
// Initialises the serial ports which will be used to communicate between the 
// arduino board and the mp3 player chip
SoftwareSerial secondarySerial(4,2); // RX, TX
typedef DFMiniMp3<SoftwareSerial, Mp3Notify> DfMp3;
DfMp3 dfmp3(secondarySerial);

// Class used to handle notifying stuff to the serial monitor
class Mp3Notify
{
public:
  static void PrintlnSourceAction(DfMp3_PlaySources source, const char* action)
  {
    if (source & DfMp3_PlaySources_Sd) 
    {
        Serial.print("SD Card, ");
    }
    if (source & DfMp3_PlaySources_Usb) 
    {
        Serial.print("USB Disk, ");
    }
    if (source & DfMp3_PlaySources_Flash) 
    {
        Serial.print("Flash, ");
    }
    Serial.println(action);
  }
  static void OnError([[maybe_unused]] DfMp3& mp3, uint16_t errorCode)
  {
    // see DfMp3_Error for code meaning
    Serial.println();
    Serial.print("Com Error ");
    Serial.println(errorCode);
  }
  static void OnPlayFinished([[maybe_unused]] DfMp3& mp3, [[maybe_unused]] DfMp3_PlaySources source, uint16_t track)
  {
    Serial.print("Play finished for #");
    Serial.println(track);  
  }
  static void OnPlaySourceOnline([[maybe_unused]] DfMp3& mp3, DfMp3_PlaySources source)
  {
    PrintlnSourceAction(source, "online");
  }
  static void OnPlaySourceInserted([[maybe_unused]] DfMp3& mp3, DfMp3_PlaySources source)
  {
    PrintlnSourceAction(source, "inserted");
  }
  static void OnPlaySourceRemoved([[maybe_unused]] DfMp3& mp3, DfMp3_PlaySources source)
  {
    PrintlnSourceAction(source, "removed");
  }
};

void setup() 
{
  Serial.begin(115200);

  Serial.println("initializing...");
  Serial.println("tesat");
  
  dfmp3.begin();
  // // You may hear popping when starting and you can remove this 
  // // call to reset() once your project is finalized
  //dfmp3.reset();

  Serial.println("initialised");

  uint16_t version = dfmp3.getSoftwareVersion();
  Serial.print("version ");
  Serial.println(version);

  uint16_t volume = dfmp3.getVolume();
  Serial.print("volume ");
  Serial.println(volume);
  dfmp3.setVolume(24);
  
  uint16_t count = dfmp3.getTotalTrackCount(DfMp3_PlaySource_Sd);
  Serial.print("files ");
  Serial.println(count);
  
  Serial.println("starting...");

  //dfmp3.playMp3FolderTrack(2);
  pinMode(4,INPUT);
  pinMode(5,INPUT);
  pinMode(6,INPUT);
  pinMode(7,INPUT);

}

void waitMilliseconds(uint16_t msWait)
{
  uint32_t start = millis();
  
  while ((millis() - start) < msWait)
  {
    // if you have loops with delays, its important to 
    // call dfmp3.loop() periodically so it allows for notifications 
    // to be handled without interrupts
    dfmp3.loop(); 
    delay(1);
  }
}

void loop() 
{
  delay(1000);
  dfmp3.playFolderTrack16(3, 1);

}
